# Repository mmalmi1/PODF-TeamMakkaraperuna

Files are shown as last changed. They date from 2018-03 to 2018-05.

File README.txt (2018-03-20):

# PODF-TeamMakkaraperuna
Repository
saku kävi täällä
mike myös

Try to edit this file if you need a reminder how to use git.

git clone "URL"
git status
git add ./ git add -A
git commit -m "viesti tähän" 
git push

git pull

esc :wq

git branch
git branch "uusi oksa"
git checkout "oksa"
git merge master
git push --set-upstream origin "päivitysoksa"

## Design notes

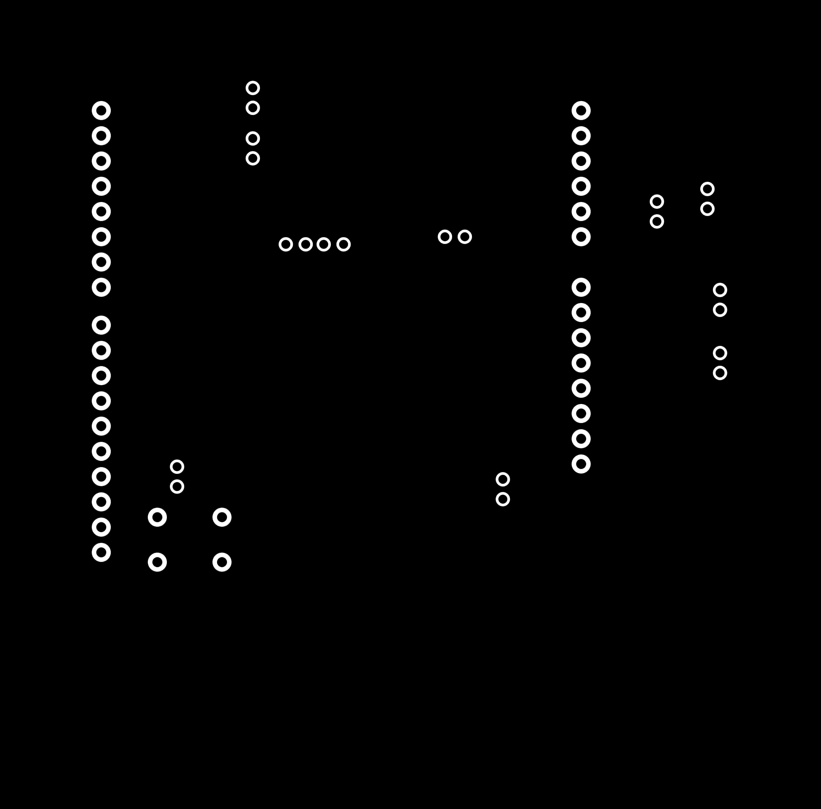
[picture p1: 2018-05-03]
Milling/pics/HolesFinal5.5.png

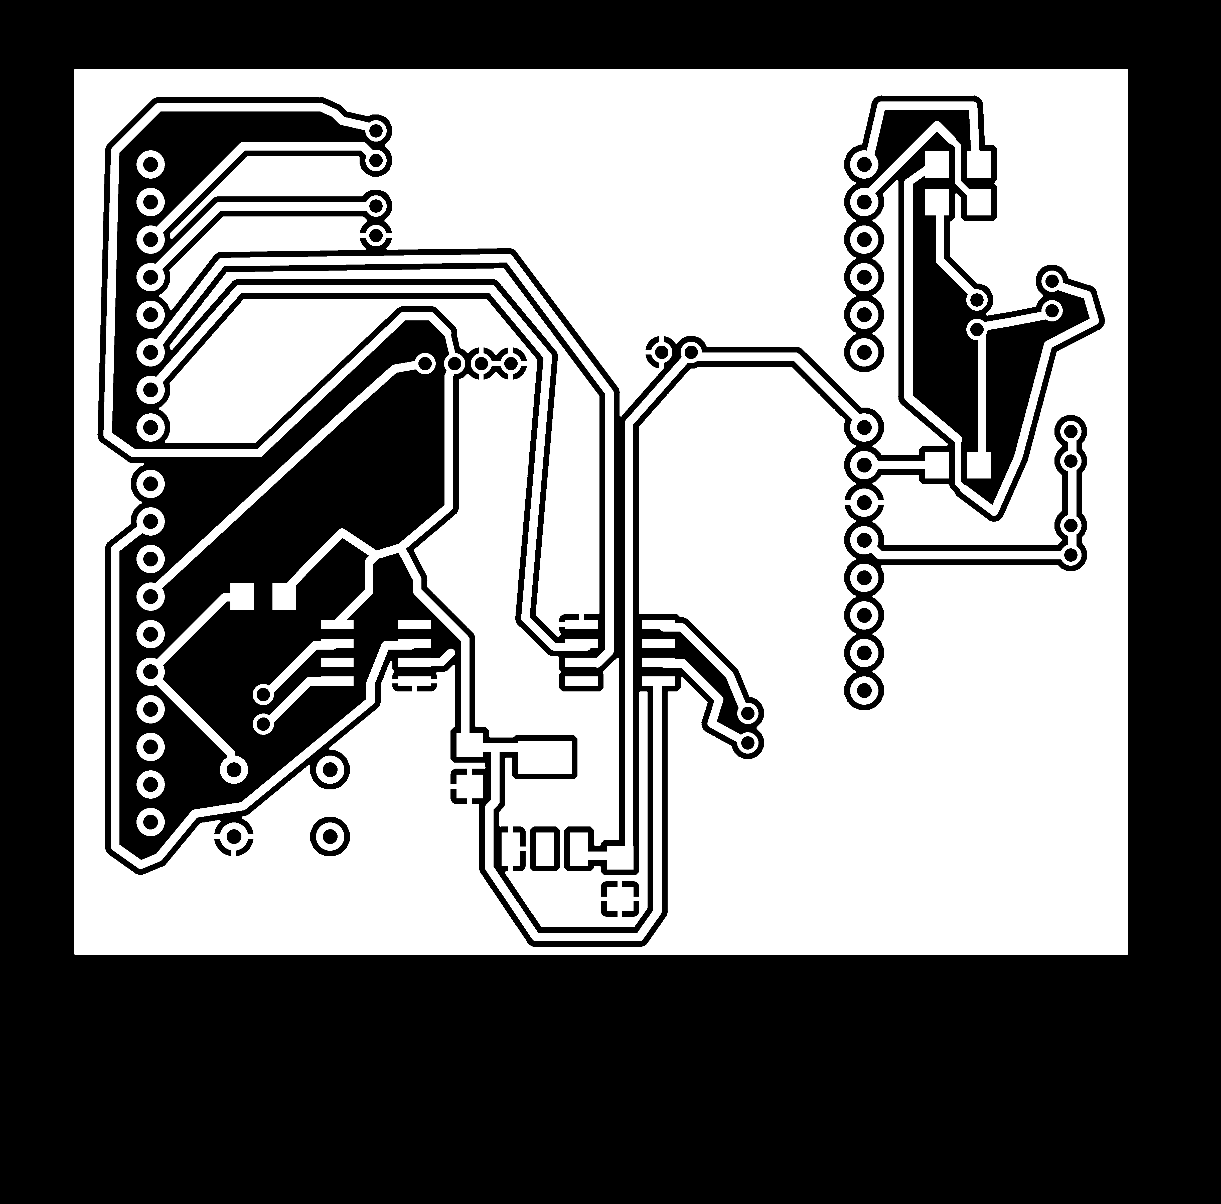
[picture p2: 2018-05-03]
Milling/pics/MillingFinal5.5.png

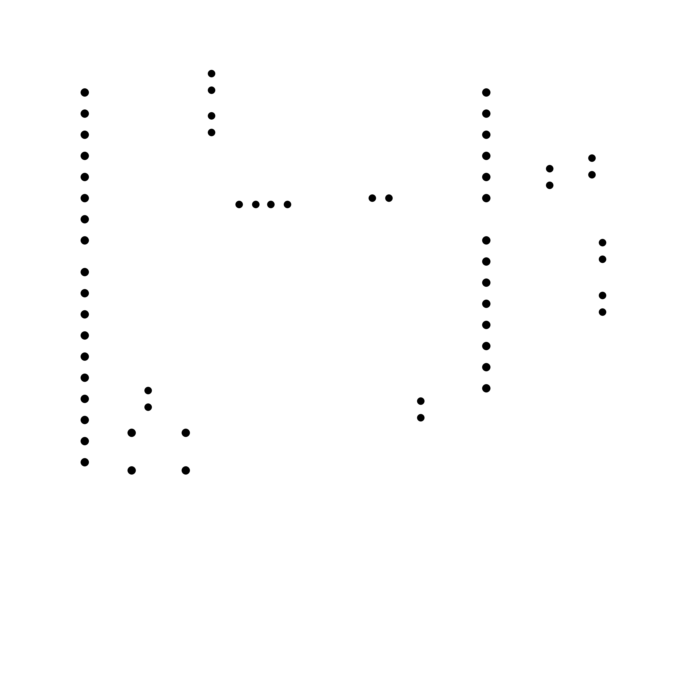
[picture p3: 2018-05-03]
Milling/pics/HolesFinal55Final.png

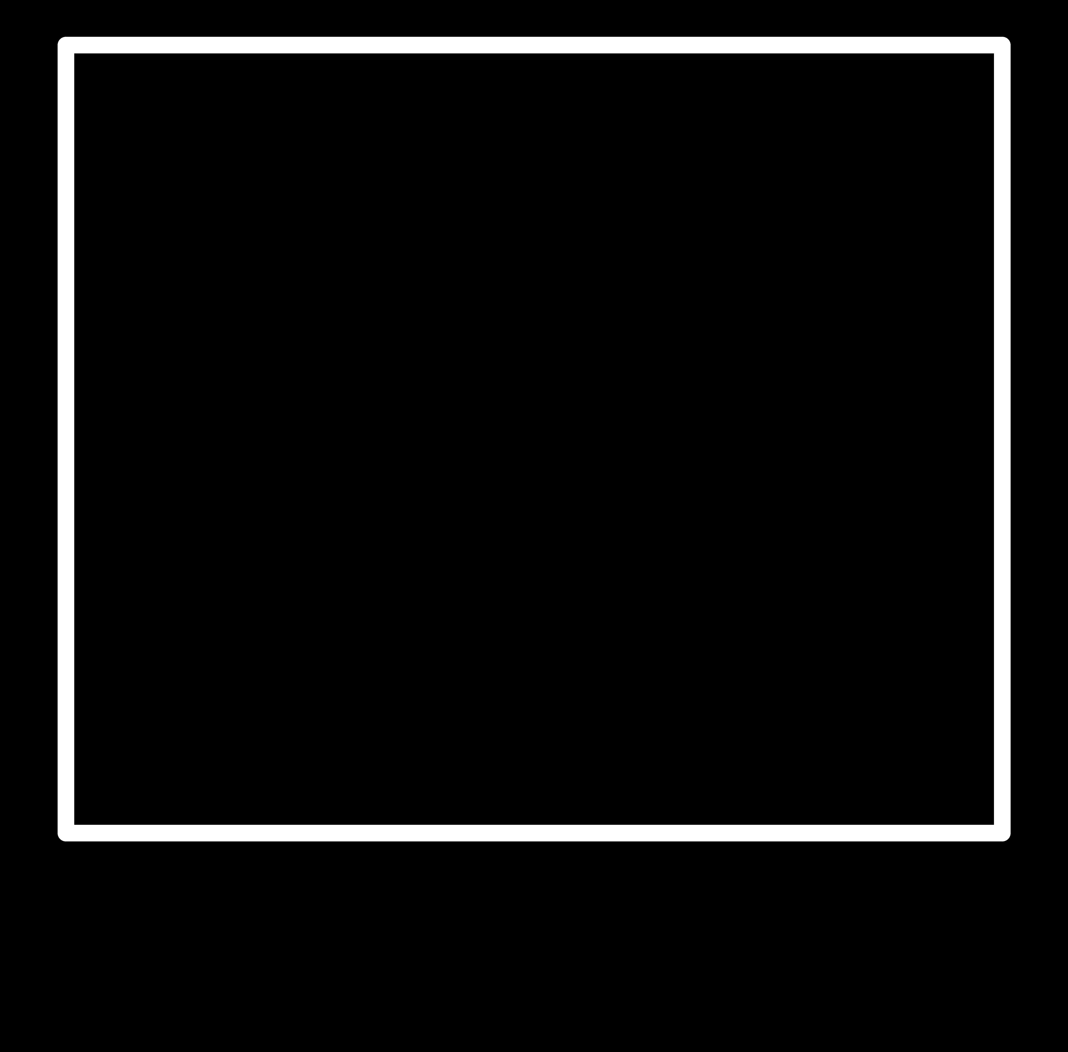
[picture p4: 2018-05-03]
Milling/pics/OutlineFinal55.png

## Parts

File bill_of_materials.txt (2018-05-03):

- 1 Arduino Uno     1050-1024-ND
- 2 H-bridge         620-1428-1-ND
- 1 Voltage Regulator     ZLDo1117G50TA
- 2 DC Motor         1568-1161-ND
- 1 Ultra Sound Sensor     1568-1421-ND
- 1 Micro servo motor     2214601
- 2 Capacitor 10 uF     587-1352-1-ND
- 6 AA Battery
- 1 Battery holder     BH26AASF-ND
- 1 Slide switch
- 1 Button
- 1 Resistor 49.9 K ohm

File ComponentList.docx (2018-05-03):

Digikey
Arduino Uno | 1050-1024-ND
H-bridge | 620-1428-1-ND
MPU-6050 (acc+gyro) | 1738-1070-ND
Voltage Regulator | ZLDo1117G50TA
Buzzer | CEM 1203
DC Motor | 1568-1161-ND
Microphone | 1568-1472-ND
Ultra Sound Sensor | 1568-1421-ND
RED Led | 160-1167-1-ND
Diode shotky | 641-1331-1-ND
Phototransistor | 1080-1380-1-ND
Capacitor 10 F | 587-1352-1-ND
Resistor 100 Ohm | 311-100FRCT-ND
Resistor 49.9K | 311-49.9KFRCT-ND
Battery cable | BS6I-MC-ND
Battery holder | BH26AASF-ND
Follow the line sensor | 1568-1554-ND
Benzine gas sensor | 605-00011-ND
RED LED | C503B-RCN-CW0Z0AA1-ND
White led | C512A-WNN-CZ0B0151-ND
Green LED | 754-1265-ND
Resistor 499 | 311-499FRCT-ND
LED strip | 1647-1018-1-ND

Jameco Micro servo motor | 2214601
DC motor | 174693

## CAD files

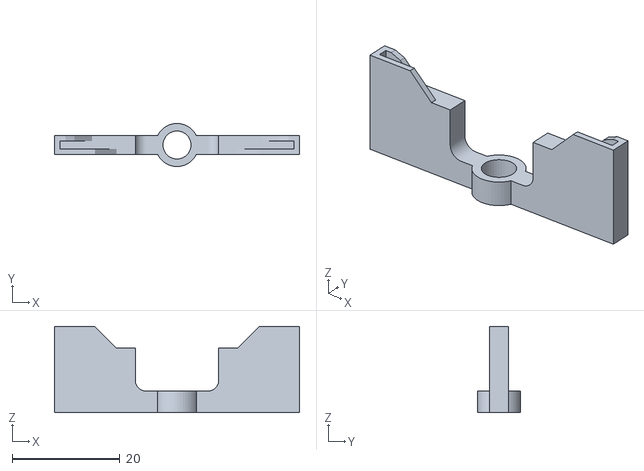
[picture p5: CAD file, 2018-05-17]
3D Printing/servo_piecev5.stl
45.5 x 8.00 x 16.0

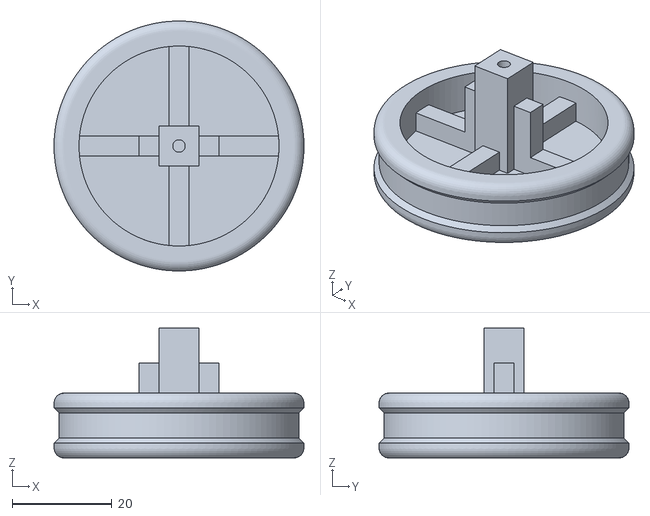
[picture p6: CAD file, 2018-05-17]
3D Printing/new_wheelv5.stl
50.0 x 50.0 x 26.0

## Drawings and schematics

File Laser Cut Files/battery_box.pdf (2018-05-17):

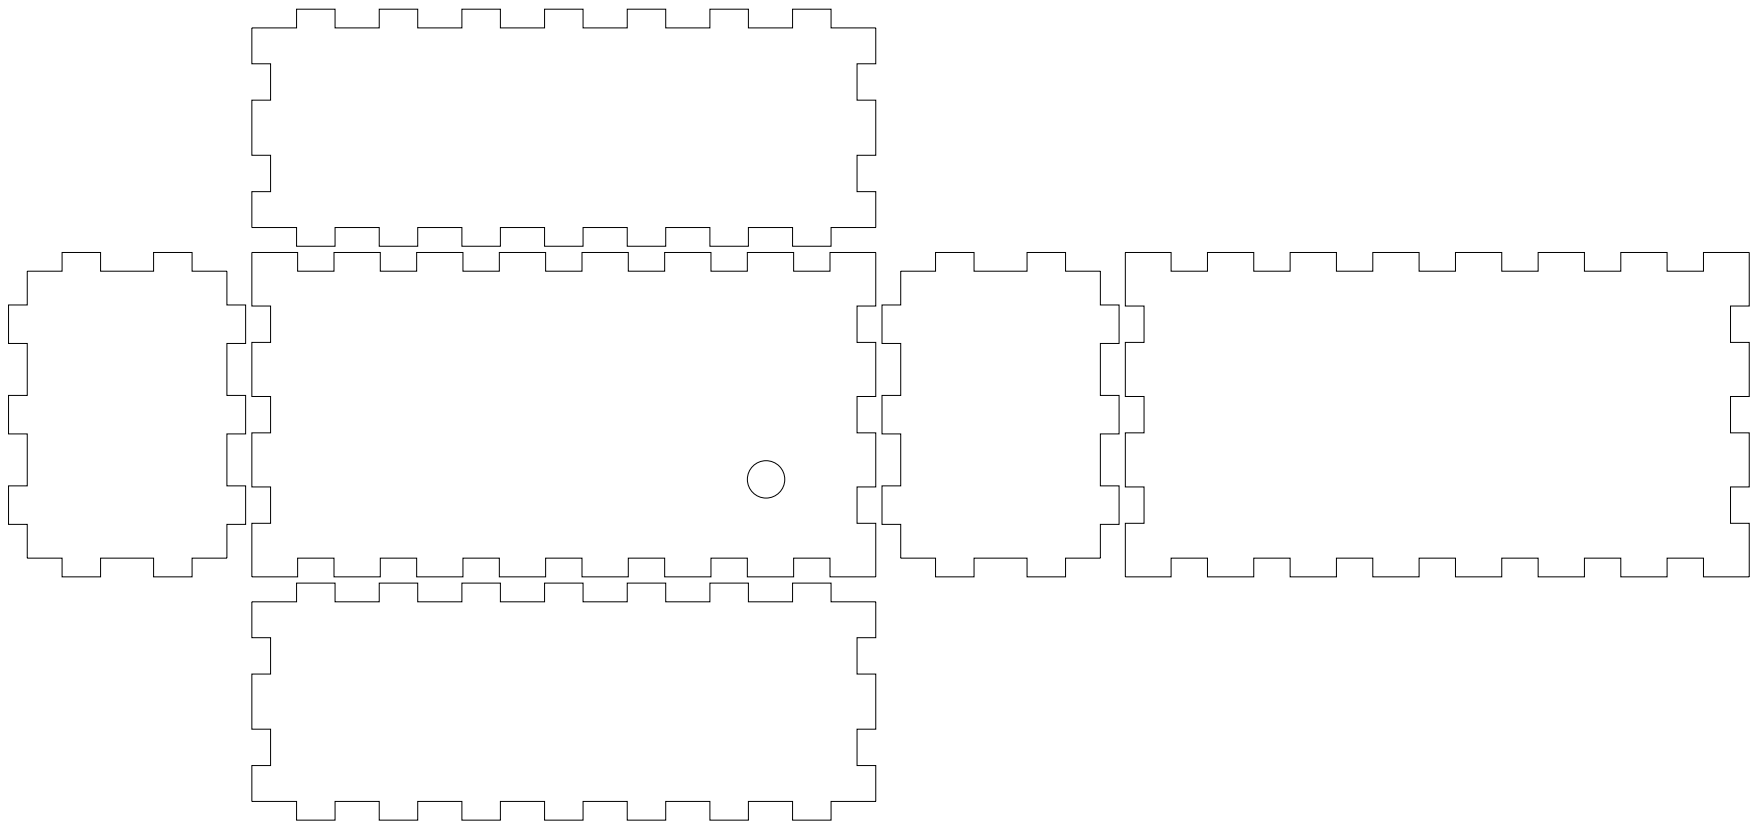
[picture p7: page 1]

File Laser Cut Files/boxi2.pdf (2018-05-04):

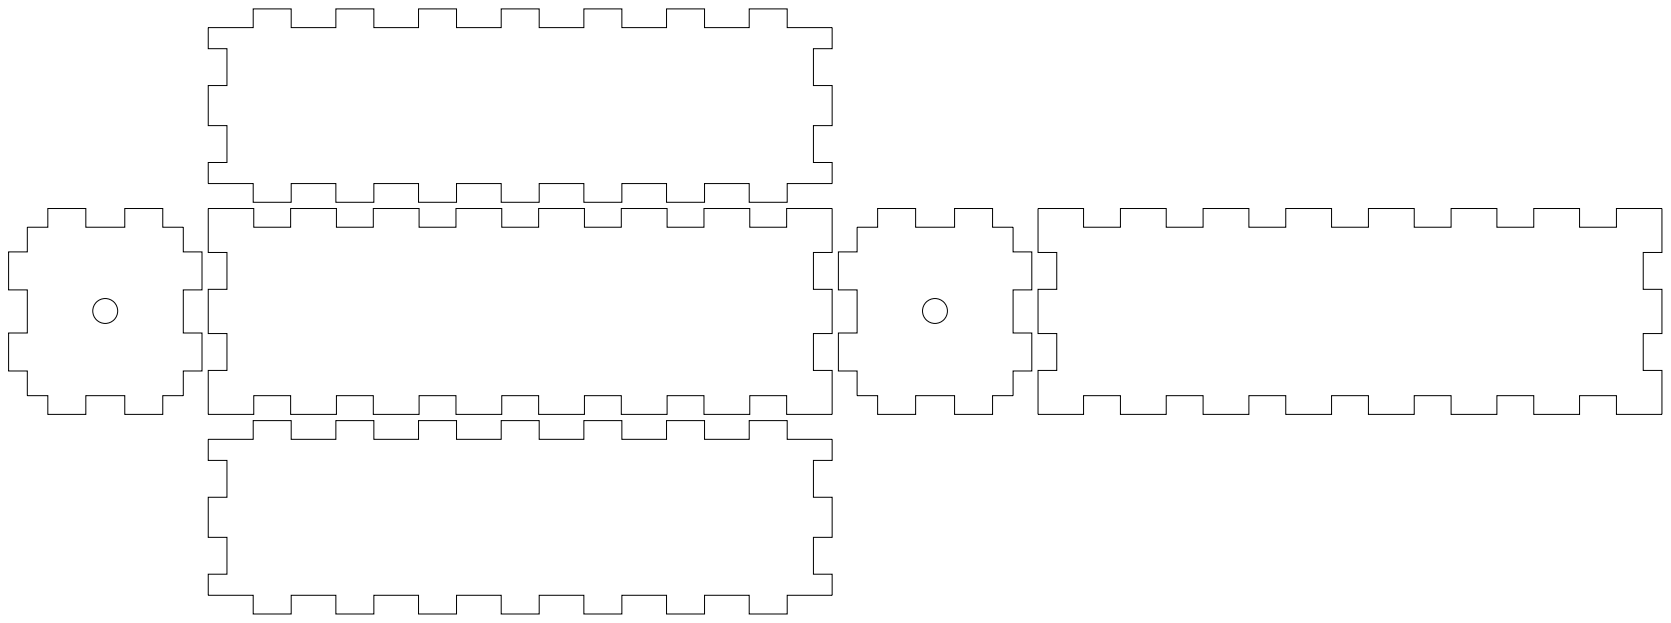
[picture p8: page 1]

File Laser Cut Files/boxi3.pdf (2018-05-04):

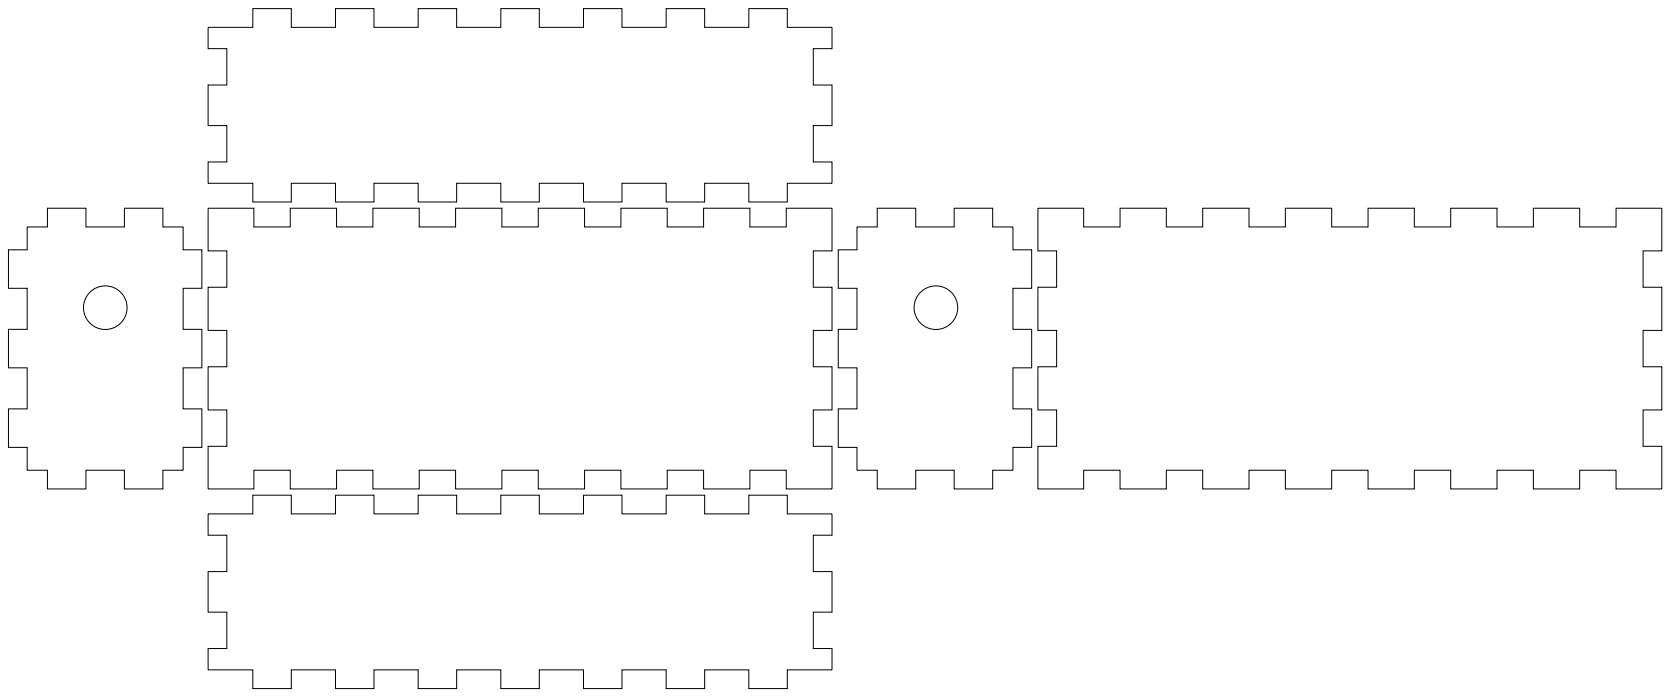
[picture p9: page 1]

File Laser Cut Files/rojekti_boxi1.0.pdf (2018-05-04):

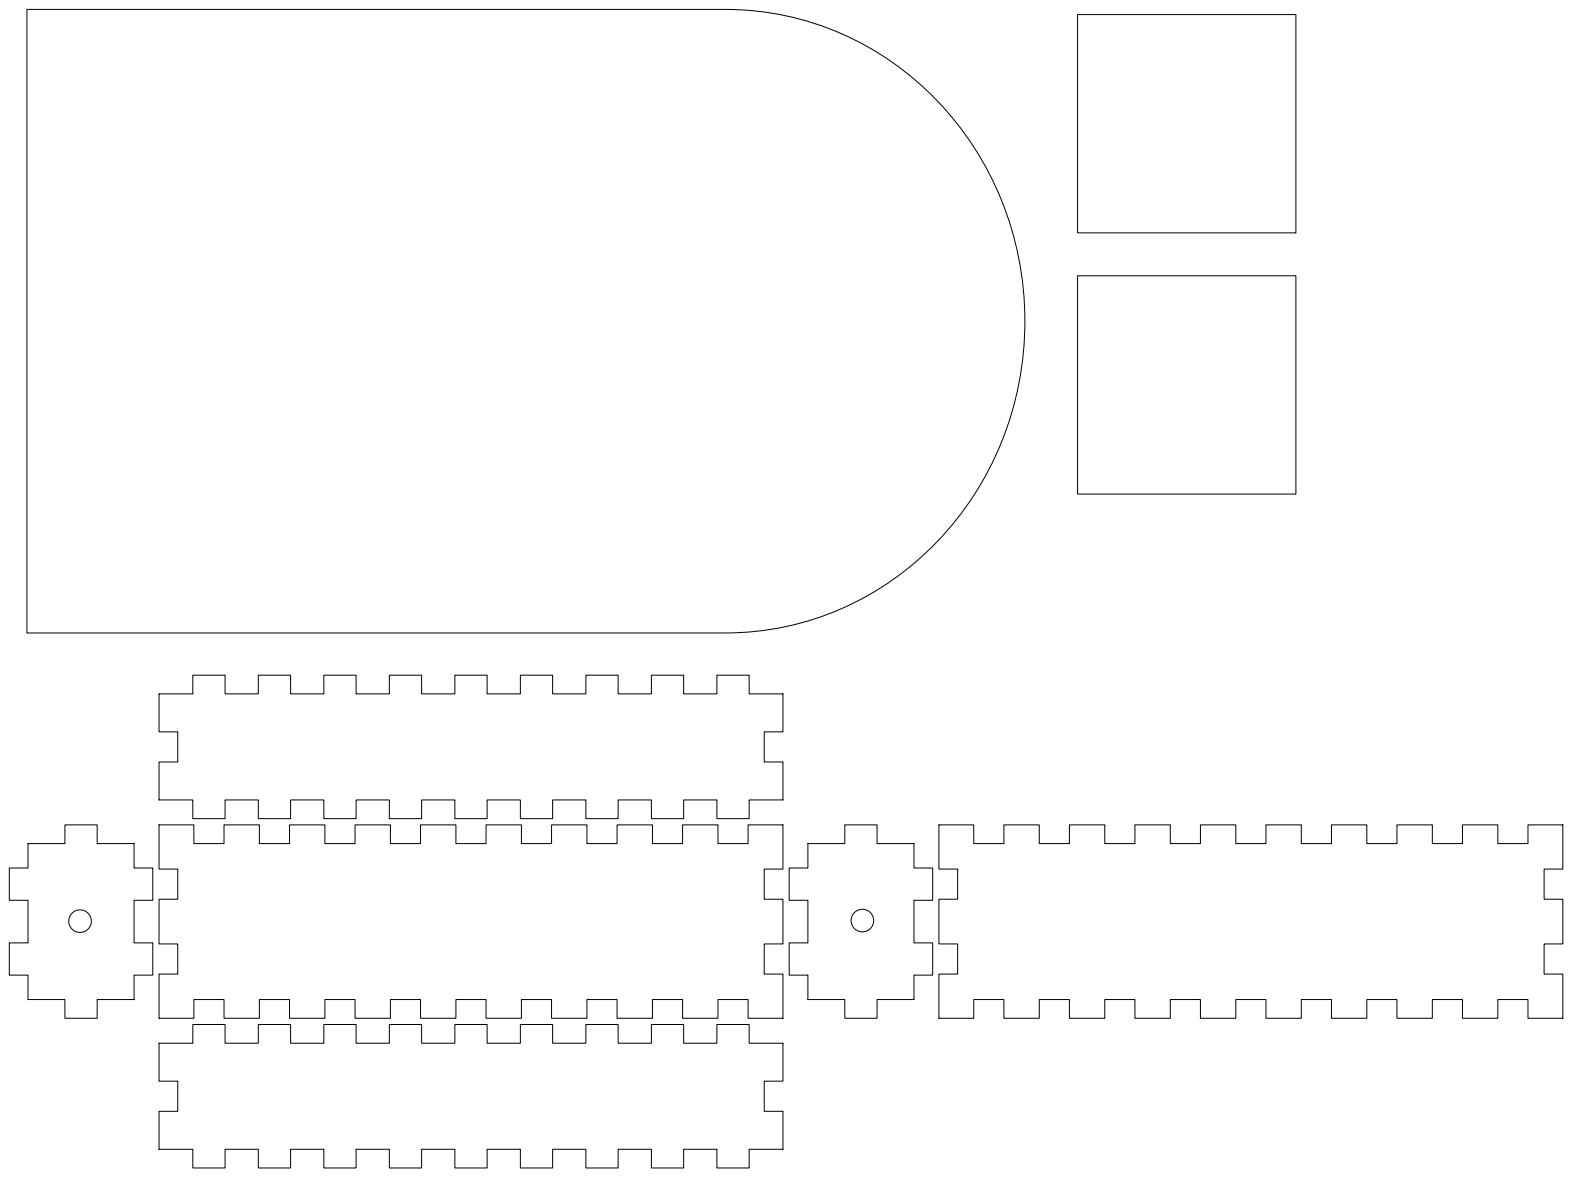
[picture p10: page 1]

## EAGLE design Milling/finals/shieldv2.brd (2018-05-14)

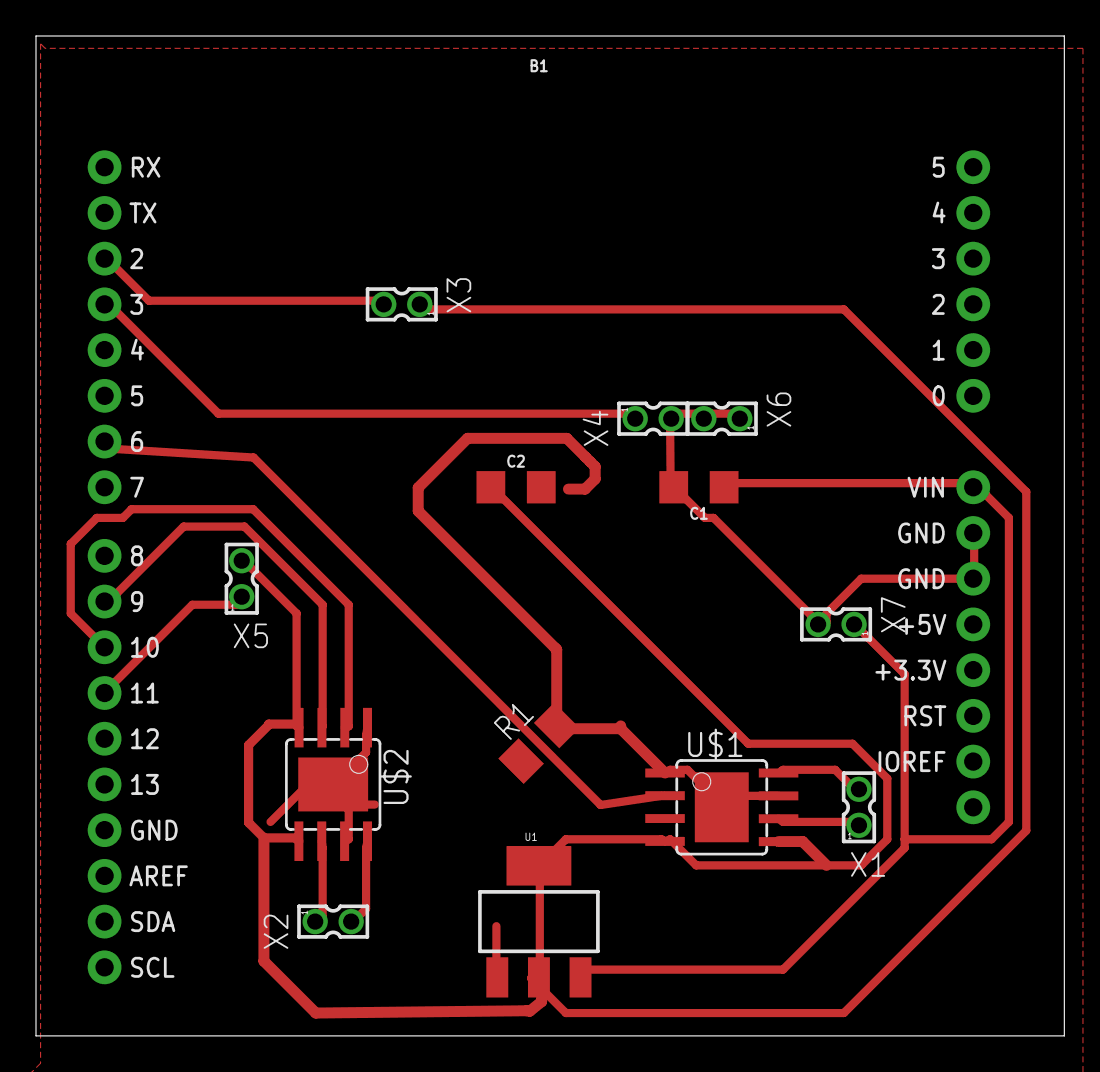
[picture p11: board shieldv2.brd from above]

Board: 2 copper layers, 57.1 x 55.6 mm, 14 parts (0 on the bottom side), 15 nets.

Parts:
B1: ARDUINO_UNO_R3_SHIELDBASIC; UNO_R3_SHIELD
C1, C2: 10uF; 1206
R1: M1206
U1: SOT223
U$1, U$2: A4953-H-BRIDGE-MOTOR-DRIVER-PAD; SOIC8_PAD
X1, X2, X3, X4, X5, X6, X7: 332-02

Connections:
+5V: C2.1, U1.2, U1.4, U$1.4, U$1.5, X3.1
unnamed: B1.GND@0, B1.GND@1, B1.GND@2, C1.2, C2.2, R1.1, R1.2, U1.1, U$1.1, U$1.7, U$1.GND, U$2.1, U$2.7, U$2.GND, X4.2, X6.1, X6.2, X7.2
unnamed: B1.D6, U$1.2
unnamed: U$1.8, X1.2
unnamed: B1.D10, U$2.2
unnamed: U$1.6, X1.1
unnamed: U$2.8, X2.2
unnamed: U$2.6, X2.1
unnamed: B1.D5, U$1.3
unnamed: B1.D3, X4.1
unnamed: B1.D2, X3.2
unnamed: B1.D11, X5.1
unnamed: B1.D9, U$2.3
S$2: U$2.4, U$2.5, X5.2
VCC: B1.VIN, C1.1, U1.3, X7.1

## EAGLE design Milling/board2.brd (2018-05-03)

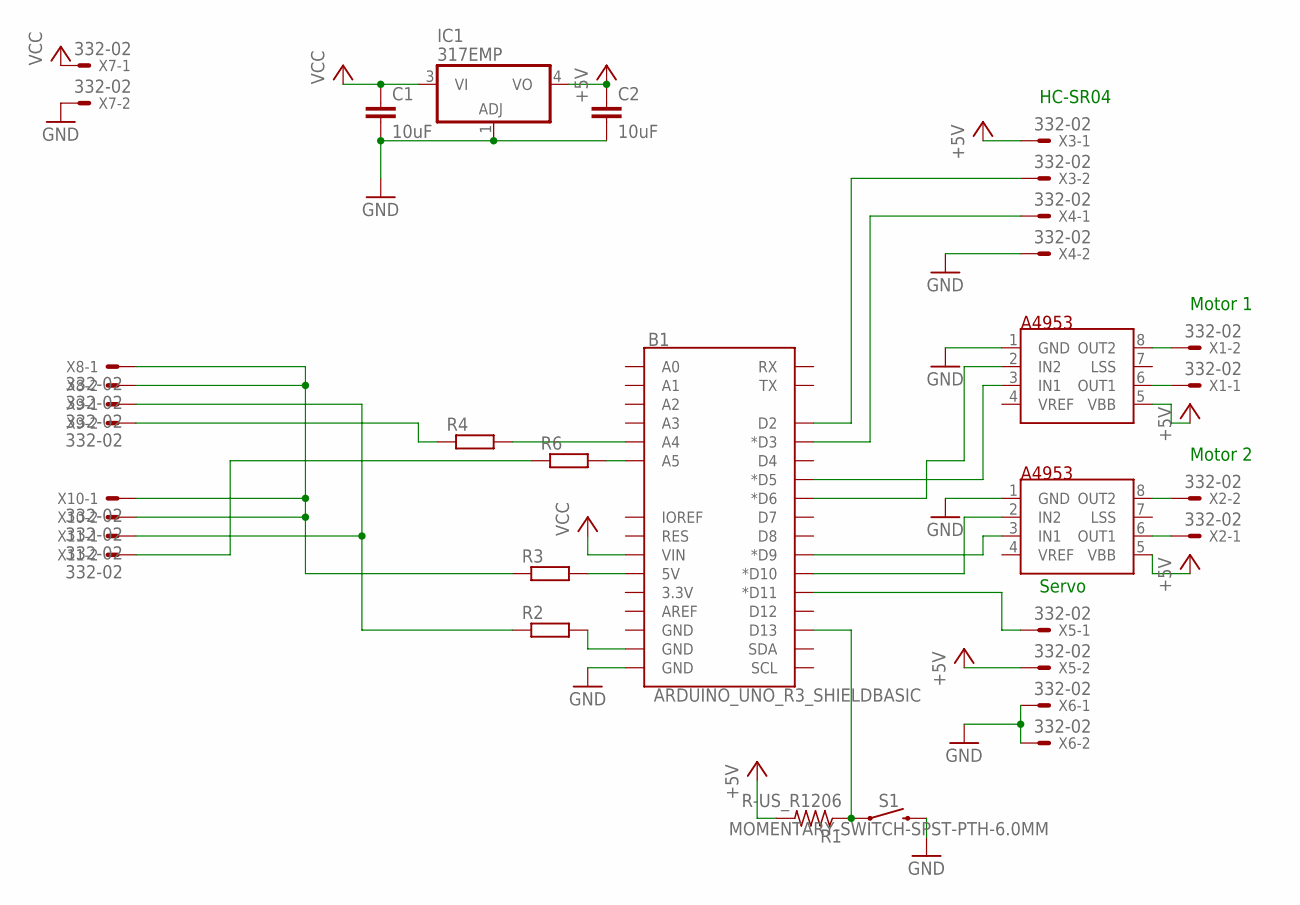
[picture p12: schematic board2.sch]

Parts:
A1, A2: A4953; SO08
B1: ARDUINO_UNO_R3_SHIELDBASIC; UNO_R3_SHIELD
C1, C2: 10uF; 1206
IC1: 317EMP; SOT223
R1: R-US_R1206; R1206
R2, R3, R4, R6: RR1206; R1206
S1: MOMENTARY-SWITCH-SPST-PTH-6.0MM; TACTILE_SWITCH_PTH_6.0MM
X1, X2, X3, X4, X5, X6, X7, X8, X9, X10, X11: 332-02

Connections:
+5V: A1.5 (VBB), A2.5 (VBB), C2.1, IC1.4 (VO), R1.2, X3.1, X5.2
GND: A1.1 (GND), A2.1 (GND), B1.GND@0 (GND), C1.2, C2.2, IC1.1 (ADJ), S1.3 (2), X4.2, X6.1, X6.2, X7.2
unnamed: A1.3 (IN1), B1.D5 (*D5)
unnamed: A1.2 (IN2), B1.D6 (*D6)
unnamed: A2.3 (IN1), B1.D9 (*D9)
unnamed: A2.2 (IN2), B1.D10 (*D10)
unnamed: A1.6 (OUT1), X1.1
unnamed: A1.8 (OUT2), X1.2
unnamed: A2.6 (OUT1), X2.1
unnamed: A2.8 (OUT2), X2.2
unnamed: B1.D3 (*D3), X4.1
unnamed: B1.D2, X3.2
unnamed: B1.D11 (*D11), X5.1
unnamed: B1.D13, R1.1, S1.1
unnamed: B1.A4, R4.2
unnamed: R3.1, X8.1, X8.2, X10.1, X10.2
unnamed: R2.1, X9.1, X11.1
unnamed: B1.GND@1 (GND), R2.2
unnamed: R4.1, X9.2
unnamed: B1.5V, R3.2
unnamed: B1.A5, R6.2
unnamed: R6.1, X11.2
VCC: B1.VIN, C1.1, IC1.3 (VI), X7.1

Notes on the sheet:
Motor 1
Motor 2
Servo
HC-SR04

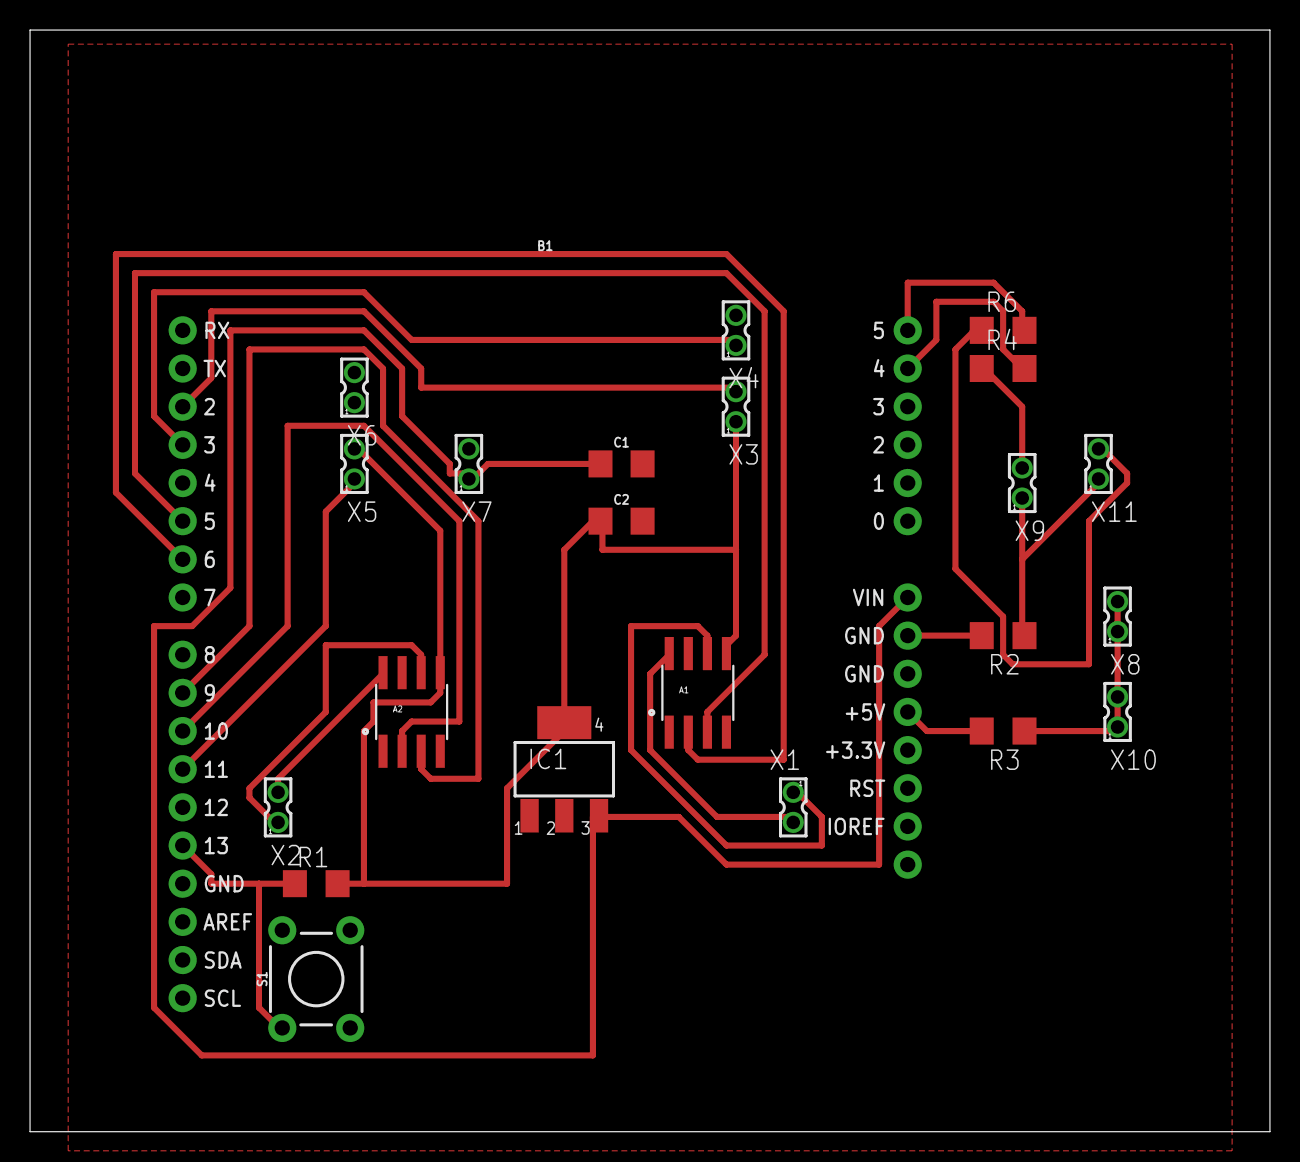
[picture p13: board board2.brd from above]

Board: 2 copper layers, 82.5 x 73.3 mm, 23 parts (0 on the bottom side), 23 nets.

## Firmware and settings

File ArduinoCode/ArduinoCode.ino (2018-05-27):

#include <hcsr04.h>
#include <Servo.h>
#include <PWM.h>
//#include <Dcmotor.h>


//outputs
int ServoPin = 11;
int Motor1In1 = 5;
int Motor1In2 = 6;
int Motor2In1 = 9;
int Motor2In2 = 10;
//int UltSensorEcho = 3;


//int UltSensorTrig = 2;
int ButtonIn = 13;


//init servo object
Servo myservo;
int ServoPos = 0;

// current wall ( 1 = left , 2 = forward, 3 = right)
int currentWall = 0;

// set wall flags
bool wallLeft = false;
bool wallForward = false;
bool wallRight = false;



#define TRIG_PIN 2
#define ECHO_PIN 3
#define INF_FORK1 A4
#define INF_FORK2 A5

//init ultsonic object with min 20 mm , max 1500mm
HCSR04 hcsr04(TRIG_PIN, ECHO_PIN, 5, 15000);
// sonicsensor min dist in mm
int SSMinDist = 1000 ;



void setup()
  {
    Serial.begin(9600);
    //InitTimersSafe();

    myservo.attach(ServoPin);
    
    //SetPinFrequencySafe(Motor1In1, 450);
   // SetPinFrequencySafe(Motor1In2, 35);

    pinMode(5,OUTPUT);
    pinMode(6,OUTPUT);
    
    
    pinMode(11,OUTPUT);
   
    pinMode(9,OUTPUT);
    pinMode(10,OUTPUT);
 
    pinMode(13, INPUT);
    pinMode(A5, INPUT);
    pinMode(A4, INPUT);  


  
  }
bool IsWall(int minDist)
{
  //Checks if wall 
  int dist = hcsr04.distanceInMillimeters();
 // Serial.println(dist);
  if(dist <= minDist && dist > 1 )
  {
   Serial.print("IsWall");
    return true;
    
    
  }
  else
  {
    //Serial.print("NOWall");
    return false;
  } 
}

void TurnLeft(int speed)
  {
    //add pwm
    analogWrite(5,speed);
    analogWrite(10,speed);
    // adjust delay
    
    delay (600);
    Serial.println("Turning Left!");
    analogWrite(5,0);
    analogWrite(10,0);
    
    //turn left 
  }
void TurnRight(int speed)
  {
    analogWrite(6,speed);
    analogWrite(9,speed);
    // adjust delay
    
    delay (400);
    Serial.println("Turning Left!");

    analogWrite(6,0);
    analogWrite(9,0);
     //turn right
  } 
 void GoForward(int speed)
	{
    //int speed2 = 225;
		analogWrite(5,200);
		analogWrite(9,speed);
	}
void Stop()
	{
    digitalWrite(5,1);
    digitalWrite(6,1);
    digitalWrite(9,1);
    digitalWrite(10,1);
    delay(100);
		digitalWrite(5,0);
		digitalWrite(6,0);
		digitalWrite(9,0);
		digitalWrite(10,0);
	}


int CheckServoDir(int AnglePos)
{
  //returns 1 for left, 2 for mid, 3 for right(or not)
  if(AnglePos <= 60)
    {
      return 1;
    }
  else if(AnglePos > 60 && AnglePos < 120)
    {
      return 2;
    }
    
  else if(AnglePos >= 120)
    {
      return 3;
    }  
}

void AvoidObs()
  {
    if (wallLeft == 0)
            {
              TurnLeft(100);
              //forward
            }
          else if(wallRight == 0)
            {
              TurnRight(100);
              //forward
            } 
  }
void SetWallFlags()
{
  //Serial.println(CheckServoDir(ServoPos));
  int wallDir = CheckServoDir(ServoPos);
  //GoForward(255);
  if(IsWall(SSMinDist) == true)
    {
      
      //if wall found set wall flags
      
	  
      if( wallDir == 1)
        {
          wallLeft = true;
		      currentWall = 1;
        }
      else if (wallDir == 2)
        {
		    	wallForward = true;
				  Stop();
		    	//stop
			    //if wall left == 0, turn left / if wallright == 0, turn right
				  
						
						TurnLeft(255);
						delay(500);
						
         /*
				else if(wallLeft == true and wallRight == false)
					{
						
						TurnRight(255);
						delay(1000);
						
					}
         */
          wallForward = false;
          
			//continue loop
        }
      if (wallDir == 3)
        {
          wallRight = true;
		  currentWall = 3;
        }  
      
    }
  else if (IsWall(SSMinDist) == false)
    {
      if( wallDir == 1)
        {
          wallLeft = false;
        }
      else if (wallDir == 2)
        {
          wallForward = false;  
        }
      else if (wallDir == 3)
        {
          wallRight = false;  
        }     
    }
  }
    

void ServoSweep()
{
    for(ServoPos = 90; ServoPos<=180; ServoPos = ServoPos + 90)
    {
        myservo.write(ServoPos);
        delay(200);
      
        SetWallFlags();
		
        Serial.print(" ");
        Serial.print(wallLeft);
        Serial.print(wallForward);
        Serial.print(wallRight);
        Serial.println("");

        delay(200);
        
        
        //Serial.println(ServoPos);
        
        //delay(250);
    } 
    
    for(ServoPos = 90; ServoPos >= 0; ServoPos = ServoPos - 90)
    {
        myservo.write(ServoPos);
        delay(200);
     
        SetWallFlags();
		
        Serial.print(" ");
        Serial.print(wallLeft);
        Serial.print(wallForward);
        Serial.print(wallRight);
        Serial.println("");
        delay(200);
        
       // delay(250);  
        
    }  
    
    
}


  

void loop() 
{
	/*
    GoForward(255);
    delay(1000);
    TurnRight(255);
    delay(1000);
    GoForward(255);
    delay(1000);
    Stop();
    
    while(true);
	*/
    
   ServoSweep();
   GoForward(255);
   
   
   //myservo.write(0);
   Serial.println(hcsr04.distanceInMillimeters());
   
 
}

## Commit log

2018-04-11 Added bill of materials
2018-04-11 Edited bill of materials
2018-05-03 Adding milling files
    [board2.brd, board2.sch]
2018-05-03 fixed eagle files
    [finalboard.brd, finalboardsch.sch]
2018-05-04 added laser cut files
2018-05-07 Made servo spin and check for walls
2018-05-14 added board file
    [shieldv2.brd, shieldv2.sch, shieldv3.brd]
2018-05-17 Added 3D printed files
    [new_wheelv5.stl, servo_piecev5.stl]

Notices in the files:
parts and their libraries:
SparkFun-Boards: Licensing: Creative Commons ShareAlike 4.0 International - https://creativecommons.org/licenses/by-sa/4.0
